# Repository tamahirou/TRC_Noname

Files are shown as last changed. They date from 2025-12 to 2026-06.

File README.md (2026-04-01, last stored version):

# TRC2027基板回路図説明書

### 0.これは回路図段階で書いたものです
# 1.メイン基板について
### 1-1.電源ブロック
DCDCコンバーターについて
| 使用モジュール | 元電源電圧 | 変換電源電圧 | 最大電流 |
| :--- | :--- | :--- | :--- |
| LMR38025 | 22.2V~25.2V | 5V | 3A |
| OKL-T/6-W12N-C | 5V | 3.3V | 6A |

電源接続コネクタ : XT90

電源最大許容電流 : 10A それ以上になるとヒューズで切れます

逆接保護 : SBDとヒューズ　逆接時ショート状態になった後ヒューズが切れることにより安全に遮断

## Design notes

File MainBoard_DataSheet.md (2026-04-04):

# TRC2027MainBoard_DataSheet

### 0.これは回路図段階で書いたものです
# 1.メイン基板について
### 1-1.電源ブロック
#### DCDCコンバーターについて
| 使用モジュール | 元電源電圧 | 変換電源電圧 | 最大電流 |
| :--- | :--- | :--- | :--- |
| LMR38025 | 22.2V~25.2V | 5V | 3A |
| OKL-T/6-W12N-C | 5V | 3.3V | 6A |

#### 電圧表示機

絶縁型DCDCコンバーターで5Vから新たな5VとGNDを生成しそれを用いることで別GNDとして電圧表示機を動作させる

#### その他

電源接続コネクタ : XT90

電源最大許容電流 : 10A それ以上になるとヒューズで切れます

逆接保護 : SBDとヒューズ　逆接時ショート状態になった後ヒューズが切れることにより安全に遮断

### 1-2.モータードライバー(DRV8262DDWRModule)

自作をしました、モジュールについては2をご覧ください

XH出力　最大電流3A

| 題 | 値 |
| :--- | :--- |
| AIN1 | GPIO6 |
| AIN2 | GPIO7 |
| BIN1 | GPIO8 |
| BIN2 | GPIO9 |
| CIN1 | GPIO10 |
| CIN2 | GPIO11 |
| DIN1 | GPIO13 |
| DIN2 | GPIO14 |
### 1-3.BNO055
| 題 | 値 |
| :--- | :--- |
| 電源電圧 | 3.3V |
| 通信方法 | I2C |
| 通信ポート | GPIO2,3|

### 1-4.GPS(MIKROE-5914)
| 題 | 値 |
| :--- | :--- |
| 電源電圧 | 5V |
| 通信方法 | I2C |
| 通信ポート | GPIO2,3 |
| リセットピン | GPIO15 |

### 1-5.気温気圧高度センサー(回路図ブロック名:Temperature, pressure, and altitude sensor)
| 題 | 値 |
| :--- | :--- |
| 電源電圧 | 5V |
| 通信方法 | I2C |
| 通信ポート | GPIO2,3 |

### 1-6.SD
| 題 | 値 |
| :--- | :--- |
| 電源電圧 | 3.3V |
| 通信方法 | SPI |
| 通信ピン | 以下の通り |
| SCK | GPIO18 |
| MISO | GPIO16 |
| MOSI | GPIO19 |
| CS | GPIO17 |

### 1-7.Lora
| 題 | 値 |
| :--- | :--- |
| 電源電圧 | 5V |
| 通信方法 | UART (1) |
| 通信ポート | GPIO4,5 |
| AUX(状態表示ピン) | GPIO12 |

モード選択:通常送受信モード: M0,M1ともにLow

### 1-8.LiDAR
| 題 | 値 |
| :--- | :--- |
| 電源電圧 | 5V |
| 通信方法 | I2C |
| 通信方法 | GPIO2,3 |

### 1-9.Camera(UnitV2 M12)
| 題 | 値 |
| :--- | :--- |
| 電源電圧 | 5V |
| 通信方法 | UART (0) |
| 通信ポート | GPIO0,1 |

### 1-10.NFC/Felica
| 題 | 値 |
| :--- | :--- |
| 電源電圧 | 5V |
| 通信方法 | I2C |
| 通信ポート | GPIO2,3 |
| 安定化 | 5VとGND間すぐに47μF |

### 1-11.FullColorLED
| 題 | 値 |
| :--- | :--- |
| 追加できるポート | なし |
### 1-12.I2C⇔UART変換
| 題 | 値 |
| :--- | :--- |
| 目的 | LTE対応のため |
| マイコン通信 | I2C |
| マイコン通信ポート | GPIO2,3 |
| LTEとの通信 | UART |
| LTEとの通信ポート | 左側7,8番ピン |

### 1-13.LTE
| 題 | 値 |
| :--- | :--- |
| 電源電圧 | 5V |
| VIO電圧 | 3.3V |
| 電源注意事項 | VINとVIOのジャンパを外す |
| RESETピン | GPIO26 |
| PWRKEYピン | GPIO27 |
| PWRKEYとは | 一定時間Lowにすると起動 |
| RESETピン＆PWRKEY | Lowにすると起動 | 
| 通信方法 | UART |
| 通信ピン | 1-12のもの |

詳しくは予算表を

# 2.自作モータードライバー基板について(DRV8262DDWModule)
| 題 | 値 | 値2 | 値3 | 値4 |
| :--- | :--- | :--- | :--- | :--- |
|仕様定義名|数値|
|定格電圧|25V|
|推奨動作電圧|24V|
|絶対最大定格電圧|50V|
|ピーク電流|16A|
|推奨連続動作電流|6A以下|
|ロジック電圧|3.3V or 5V|
|最大電流設定|無効化(フルパワー出力)|
|DECAYモード|スローディケイ(ブレーキまたはハイサイド還流)
|PWMオフ時間(TOFFピン)|7μs(TOFFをGNDに接地)|
|フォルトからの回復方法|自動的に通常動作に復帰|
|フォルト通知|VM定電流|VCP定電圧|過電流|サーマルシャットダウン|
|ブリッジモード|シングルHブリッジ|
|制御方法|PWM制御|
|nSLEEPピンの状態|常にHigh→デバイスが常にイネーブル|
|サーマルパッド|GND接続|
|安定化コンデンサ|470μF|100μなどでもいいですが、6Aまで持たせるため470μ|
|おすすめ銅箔の厚さ|2oz|
|ビア処理|レジスト開口|
|熱耐久|理論上は6A30分でも熱保護働かず耐え|
|VM,GNDコネクタ|XT30|
|OUT1,2コネクタ|XT30|
|その他コネクタ|JST XHコネクタ|
|熱対策|サーマルビアをパッドに32個|様々な配線にサーマルビア|

## ICのデータシート
[https://www.ti.com/document-viewer/ja-jp/DRV8262/datasheet]

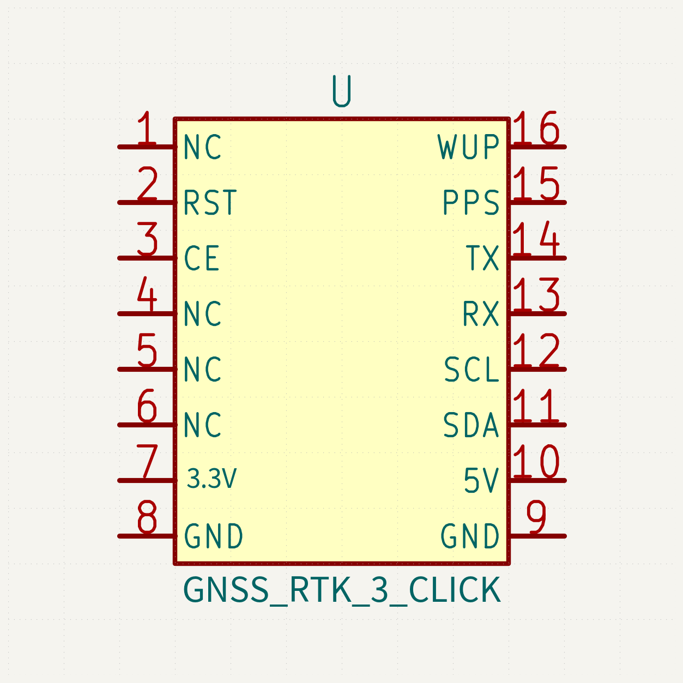
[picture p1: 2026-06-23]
TRC2027/TRC2027main2/GNSSRTK3/previews/GNSS_RTK_3_Click_symbol_preview.png

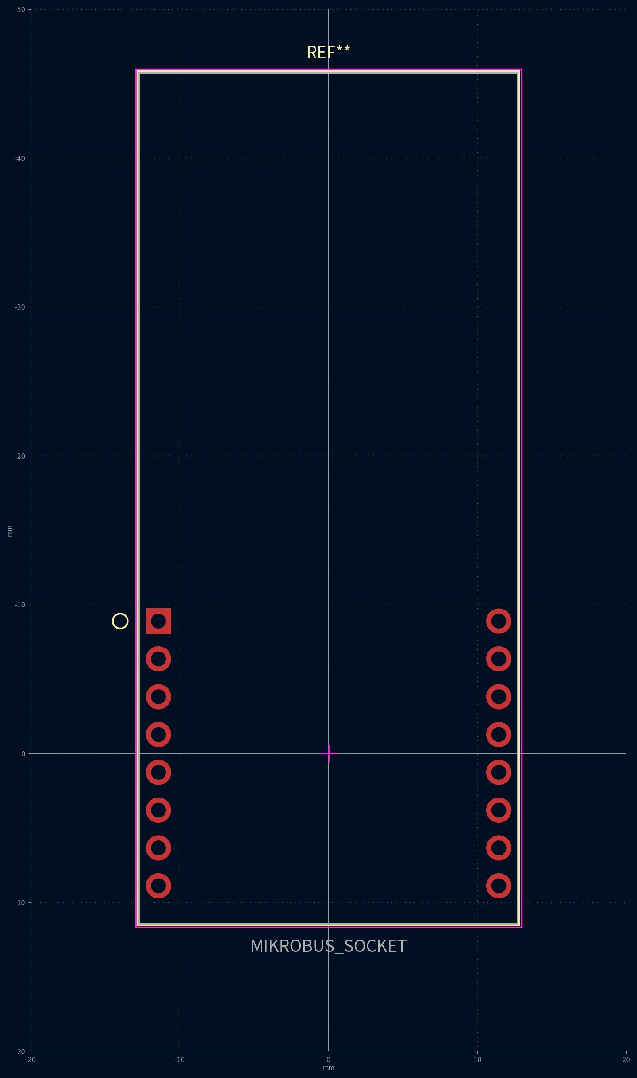
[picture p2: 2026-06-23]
TRC2027/TRC2027main2/GNSSRTK3/previews/MIKROBUS_SOCKET_footprint_preview.png

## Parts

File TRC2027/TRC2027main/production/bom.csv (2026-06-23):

Designator | Footprint | Quantity | Value | LCSC Part #
AMOTER, CMOTER, J5 | JST_XH_B2B-XH-A_1x02_P2.50mm_Vertical | 3 | XH_Moter_Output
C1 | CAPPRD500W65D1000H1300 | 1 | 470μF
C11, C9 | CP_Radial_D8.0mm_P3.50mm | 2 | 100u
C2, C5_0.1U | 0603 | 2 | 0.1μF
C4 | CP_Radial_D8.0mm_P3.50mm | 1 | 100μF
C6 | 0603 | 1 | 22u
C7 | CP_Radial_D8.0mm_P3.50mm | 1 | C7_100u
C8 | 0603 | 1 | 10u
D1 | LED_D5.0mm | 1 | 5V抵抗内蔵
D2 | LED_D5.0mm | 1 | 3.3V抵抗内蔵
D8 | TO255P480X1000X2050-3P | 1 | MBR3045FCT
DMOTER | JST_XH_B2B-XH-A_1x02_P2.50mm_Vertical | 1 | DMoter
F2 | FUSE_3557-15 | 1 | 3557-15
J1 | AMASS_XT90PW-M_1x02_P10.90mm_Horizontal | 1 | Power_conn(XT90)
J28 | JST_XH_B3B-XH-A_1x03_P2.50mm_Vertical | 1 | Servo_1
J30 | JST_XH_B20B-XH-A_1x20_P2.50mm_Vertical | 1 | Conn_01x20_Pin
MD1 | OKL-T&slash_6-W12N-C-Kai | 1 | OKL-T_6-W12N-C | OKL-T/6-W12N-C
PS1 | MAU101 | 1 | MAU102_電圧計用切り離し
R1 | R_Axial_DIN0207_L6.3mm_D2.5mm_P10.16mm_Horizontal | 1 | 1.5k
R2 | R_Axial_DIN0207_L6.3mm_D2.5mm_P10.16mm_Horizontal | 1 | 680
R3 | R_Axial_DIN0207_L6.3mm_D2.5mm_P10.16mm_Horizontal | 1 | 1.2k
SERVO_2, SERVO_3 | JST_XH_B3B-XH-A_1x03_P2.50mm_Vertical | 2 | Conn_01x03_Pin
SW1 | AMASS_XT90PW-M_1x02_P10.90mm_Horizontal | 1 | SW_SPST
U1 | LM70880Module | 1 | ~
U2, U3, U4, U5 | DRV8262DDWRModule | 4 | DRV8262DDWR
測定電圧 | JST_XH_B2B-XH-A_1x02_P2.50mm_Vertical | 1 | 電圧計_測定
電源供給 | JST_XH_B2B-XH-A_1x02_P2.50mm_Vertical | 1 | 電圧計_電源

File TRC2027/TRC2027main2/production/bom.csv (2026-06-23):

Designator | Footprint | Quantity | Value | LCSC Part #
_2, |  | 2
A1 | RaspberryPi_Pico_Common_Unspecified | 1 | RaspberryPi_Pico
C3 | CP_Radial_D5.0mm_P2.00mm | 1 | 47u
D10, D11, D12, D13, D3, D4, D5, D6, D7, D9 | UCLAMP3381PTFT | 10 | UCLAMP3381P.TFT
IC1 | DIP794W56P254L3486H508Q28N | 1 | MCP23017-E_SP
J10 | PinSocket_1x07_P2.54mm_Vertical | 1 | Memory
J11, J7 | PinSocket_1x04_P2.54mm_Vertical | 2 | BNO055
J12 | PinSocket_1x07_P2.54mm_Vertical | 1 | Temperature, pressure, and altitude sensor
J13 | PinHeader_1x03_P2.54mm_Vertical | 1 | Conn_01x03_Pin
J14, J15, J16, J17, J18, J21, J24, J25 | JST_XH_B4B-XH-A_1x04_P2.50mm_Vertical | 8 | Conn_01x04_Pin
J19 | PinHeader_1x12_P2.54mm_Vertical | 1 | Conn_01x12_Pin
J20 | PinHeader_1x10_P2.54mm_Vertical | 1 | Conn_01x10_Pin
J30 | JST_XH_B20B-XH-A_1x20_P2.50mm_Vertical | 1 | Conn_01x20_Pin
J6 | PinHeader_1x07_P2.54mm_Vertical | 1 | Conn_01x07_Pin
J8, J9 | PinHeader_1x08_P2.54mm_Vertical | 2 | Conn_01x08_Pin
R10 | R_Axial_DIN0207_L6.3mm_D2.5mm_P10.16mm_Horizontal | 1 | 75
R11 | R_Axial_DIN0207_L6.3mm_D2.5mm_P10.16mm_Horizontal | 1 | 10k
R4, R9 | R_Axial_DIN0207_L6.3mm_D2.5mm_P10.16mm_Horizontal | 2 | 330
R5, R6, R7, R8 | R_Axial_DIN0207_L6.3mm_D2.5mm_P10.16mm_Horizontal | 4 | 10
S1 | ST12303FCG | 1 | ST12-303FCG

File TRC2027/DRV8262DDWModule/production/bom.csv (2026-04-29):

Designator | Footprint | Quantity | Value | LCSC Part #
C1 | 0603 | 1 | 1u
C2 | 0603 | 1 | 0.01u
C3 | CP_Radial_D10.0mm_P5.00mm | 1 | 470u
C4 | 0603 | 1 | 0.1u
D1 | LED_D5.0mm | 1 | LED
J1, J2 | AMASS_XT30PW-F_1x02_P2.50mm_Horizontal | 2 | XT30
J3 | JST_XH_B5B-XH-A_1x05_P2.50mm_Vertical | 1 | Conn_01x05_Pin
R1 | 1206 | 1 | 10k
R2 | R_Axial_DIN0207_L6.3mm_D2.5mm_P10.16mm_Horizontal | 1 | 4.7k
U1 | HTSSOP44-DDW_TEX | 1 | DRV8262DDWR

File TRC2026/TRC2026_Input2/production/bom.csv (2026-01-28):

Designator | Footprint | Quantity | Value | LCSC Part #
C3 | 0603 | 1 | 0.1μF
D15 | LED_D5.0mm | 1 | 5V抵抗内蔵LED
D2, D7 | LED_D5.0mm | 2 | BLUELED
D3, D4 | LED_D5.0mm | 2 | GREENLED
D5, D6 | LED_D5.0mm | 2 | REDLED
J1 | PinHeader_1x06_P2.54mm_Vertical | 1 | ジョイスティック
J2 | PinHeader_1x06_P2.54mm_Vertical | 1 | Conn_01x06_Pin
J3, J5, J6 | PinHeader_1x05_P2.54mm_Vertical | 3 | Conn_01x05_Pin
J4 | PinHeader_1x05_P2.54mm_Vertical | 1 | 1F接続
R10, R11, R12, R9 | R_Axial_DIN0207_L6.3mm_D2.5mm_P10.16mm_Horizontal | 4 | 10Ω
R7, R8 | R_Axial_DIN0207_L6.3mm_D2.5mm_P10.16mm_Horizontal | 2 | 470Ω
SW1, SW2, SW3, SW4 | TVGP01G73BB | 4 | SW_Push
SW5 | 3MS1J102M2QES | 1 | SW_SPDT

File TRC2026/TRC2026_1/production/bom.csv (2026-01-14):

Designator | Footprint | Quantity | Value | LCSC Part #
A1 | RaspberryPi_Pico_Common_Unspecified | 1 | RaspberryPi_Pico
A2 | RaspberryPi_PicoW_Common_THT | 1 | RaspberryPi_Pico_W
C1, C6, C7, C8 | CP_Radial_D8.0mm_P3.50mm | 4 | 100μF
C3 | 0603 | 1 | 0.1μF
D10, D11, D12, D13, D14, D9 | SOD2513X114N | 6 | UCLAMP3381P.TFT
D15 | LED_D5.0mm | 1 | 5V抵抗内蔵LED
J1, J15, J16, J17 | PinHeader_1x04_P2.54mm_Vertical | 4 | 2F接続
J10 | PinSocket_1x07_P2.54mm_Vertical | 1 | メモリ
J11 | PinSocket_1x04_P2.54mm_Vertical | 1 | BNO055
J12 | PinSocket_1x07_P2.54mm_Vertical | 1 | 気温気圧高度センサ
J13, J14, J18 | JST_XH_B4B-XH-A_1x04_P2.50mm_Vertical | 3 | Conn_01x04_Pin
J19 | JST_XH_B3B-XH-A_1x03_P2.50mm_Vertical | 1 | サーボ1
J2 | PinHeader_1x08_P2.54mm_Vertical | 1 | Aモータードライバー
J20 | JST_XH_B3B-XH-A_1x03_P2.50mm_Vertical | 1 | サーボ2
J21 | JST_XH_B3B-XH-A_1x03_P2.50mm_Vertical | 1 | サーボ3(予備)
J22 | PinSocket_1x12_P2.54mm_Vertical | 1 | LoRa
J23 | PinSocket_1x12_P2.54mm_Vertical | 1 | Conn_01x12_Pin
J3 | JST_XH_B2B-XH-A_1x02_P2.50mm_Vertical | 1 | Aモーター出力
J4 | PinHeader_1x08_P2.54mm_Vertical | 1 | Bモータードライバー
J5 | JST_XH_B2B-XH-A_1x02_P2.50mm_Vertical | 1 | Bモーター出力
J6 | PinHeader_1x04_P2.54mm_Vertical | 1 | Conn_01x04_Pin
J7 | PinSocket_1x04_P2.54mm_Vertical | 1 | GPS
J8, J9 | PinHeader_1x08_P2.54mm_Vertical | 2 | Conn_01x08_Pin
R1, R4 | R_Axial_DIN0207_L6.3mm_D2.5mm_P10.16mm_Horizontal | 2 | 1.5Ω
R2, R3, R5, R6 | 1210 | 4 | 0.1Ω

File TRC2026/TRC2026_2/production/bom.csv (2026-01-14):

Designator | Footprint | Quantity | Value | LCSC Part #
C1 | CAPPRD500W65D1000H1300 | 1 | 470μF
C2, C5 | 0603 | 2 | 0.1μF
C4 | CP_Radial_D8.0mm_P3.50mm | 1 | 100μF
D1 | LED_D5.0mm | 1 | 5V抵抗内蔵LED
D2, D3, D4, D5, D6, D7 | LED_D5.0mm | 6 | LED
D8 | TO255P480X1000X2050-3P | 1 | MBR3045FCT
F2 | FUSE_3557-15 | 1 | 3557-15
J1 | AMASS_XT90PW-M_1x02_P10.90mm_Horizontal | 1 | Conn_01x02_Pin
J15 | PinSocket_1x04_P2.54mm_Vertical | 1 | Conn_01x04_Pin
J16 | JST_XH_B2B-XH-A_1x02_P2.50mm_Vertical | 1 | デジタル電圧計(測定)
J17 | JST_XH_B2B-XH-A_1x02_P2.50mm_Vertical | 1 | デジタル電圧計(電力供給)
J2, J3, J4, J5, J6 | PinHeader_1x04_P2.54mm_Vertical | 5 | Conn_01x04_Pin
R10, R11, R12, R9 | R_Axial_DIN0207_L6.3mm_D2.5mm_P10.16mm_Horizontal | 4 | 10Ω
R13 | R_Axial_DIN0516_L15.5mm_D5.0mm_P20.32mm_Horizontal | 1 | 0.33Ω(熱くなります。基板取り付け時は地面から離しましょう)
R7, R8 | R_Axial_DIN0207_L6.3mm_D2.5mm_P10.16mm_Horizontal | 2 | 470Ω
SW1 | AMASS_XT90PW-M_1x02_P10.90mm_Horizontal | 1 | SW_SPST
SW2 | 3MS1J102M2QES | 1 | SW_SPDT
U1 | LMR | 1 | DCDC

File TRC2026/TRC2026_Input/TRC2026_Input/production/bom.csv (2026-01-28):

Designator | Footprint | Quantity | Value | LCSC Part #
A1 | RaspberryPi_Pico_Common_Unspecified | 1 | RaspberryPi_Pico_W
C1, C6 | 0603 | 2 | 0.1μF
C2, C4, C5 | CP_Radial_D8.0mm_P3.50mm | 3 | 100μF
J22 | PinSocket_1x12_P2.54mm_Vertical | 1 | LoRa
J23 | PinSocket_1x12_P2.54mm_Vertical | 1 | Conn_01x12_Pin
J3, J4, J5, J6 | PinHeader_1x05_P2.54mm_Vertical | 4 | 2F接続

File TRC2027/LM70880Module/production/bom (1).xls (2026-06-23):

Comment | Designator | Footprint | JLCPCB Part #
LM70880RRXR | U1 | RRX0029B-MFG | C41525220
47n | C10 | 0603 | C1622
19.1k | R4 | 0603 | C22897
24.9k | R3 | 0603 | C25962
5m | R9 | 1206 | C7419996
6.8n | C7 | 0603 | C1631
4.7u | C1,C2,C3,C4,C6 | 0805 | C76651
3.3u | L1 | SMMS10505R6M | C128687
Conn_01x02_Pin | J1,J2 | AMASS_XT30PW-F_1x02_P2.50mm_Horizontal | C2913282
1 | R8 | 0603 | C22936
47p | C8 | 0603 | C1671
5.76k | R5 | 0603 | C2933239
0.1u | C5,C9 | 0603 | C14663
47u | C11,C12,C13,C14 | 0603 | C140782
54.9k | R7 | 0603 | C23077
29.4k | R6 | 0603 | C2930086
100k | R1 | 0603 | C25803
20.5k | R2 | 0603 | C2930074

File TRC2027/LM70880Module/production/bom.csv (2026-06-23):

Designator | Footprint | Quantity | Value | LCSC Part #
C1, C2, C3, C4, C6 | 0805 | 5 | 4.7u
C10 | 0603 | 1 | 47n
C11, C12, C13, C14 | 0603 | 4 | 47u
C5, C9 | 0603 | 2 | 0.1u
C7 | 0603 | 1 | 6.8n
C8 | 0603 | 1 | 47p
J1, J2 | AMASS_XT30PW-F_1x02_P2.50mm_Horizontal | 2 | Conn_01x02_Pin
L1 | SMMS10505R6M | 1 | 3.3u
R1 | 0603 | 1 | 100k
R2 | 0603 | 1 | 20.5k
R3 | 0603 | 1 | 24.9k
R4 | 0603 | 1 | 19.1k
R5 | 0603 | 1 | 5.76k
R6 | 0603 | 1 | 29.4k
R7 | 0603 | 1 | 54.9k
R8 | 0603 | 1 | 1
R9 | 1206 | 1 | 5m
U1 | RRX0029B-MFG | 1 | LM70880RRXR

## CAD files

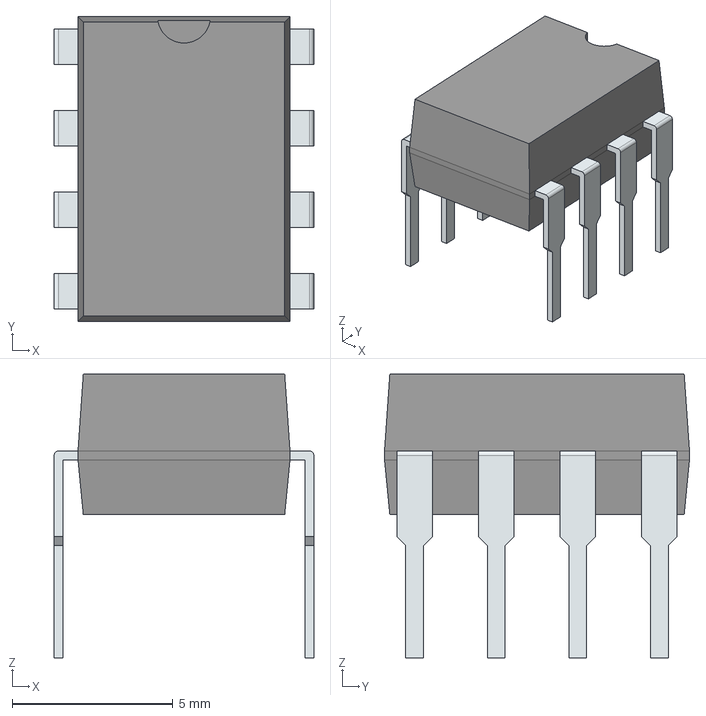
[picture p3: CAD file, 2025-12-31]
TRC2026/TRC2026_1/KiCad_24FC1025-I_P/3D/24FC1025-I_P.stp
8.09 x 9.50 x 8.83 mm
PinsArrayLR

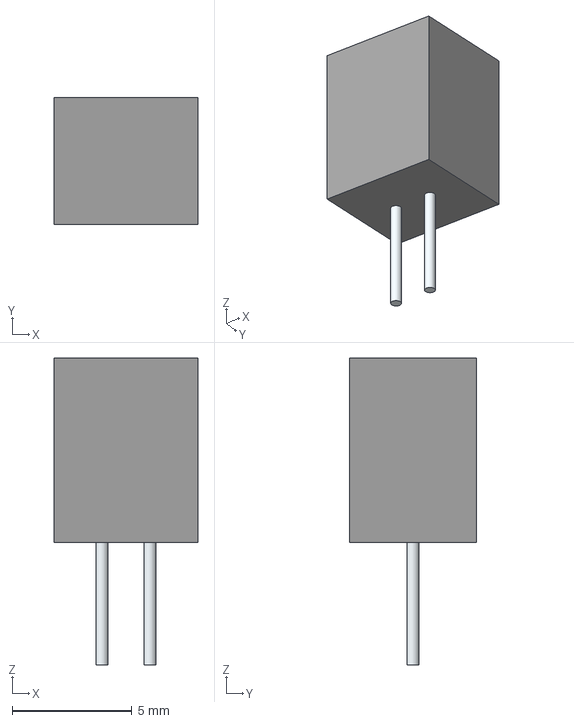
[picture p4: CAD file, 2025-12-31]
TRC2026/TRC2026_1/Kicad_B02B-PASK_LF__SN_/3D/B02B-PASK_LF__SN_.stp
6.00 x 5.30 x 12.8 mm
Leads

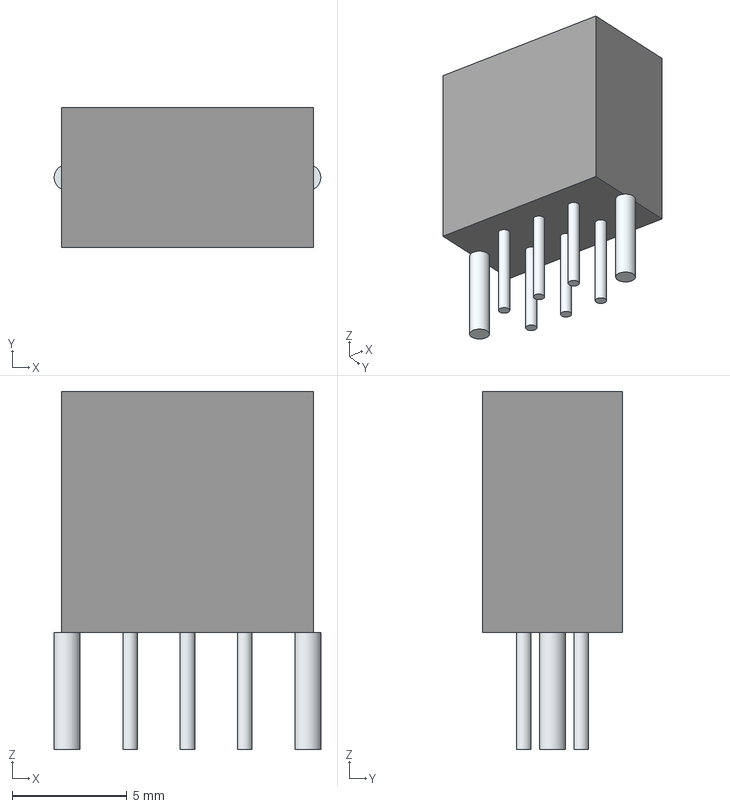
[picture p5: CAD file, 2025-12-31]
TRC2026/TRC2026_1/Kicad_switch_SS22E01G5-HA-G/3D/SS22E01G5-HA-G.stp
11.6 x 6.10 x 15.6 mm
Leads

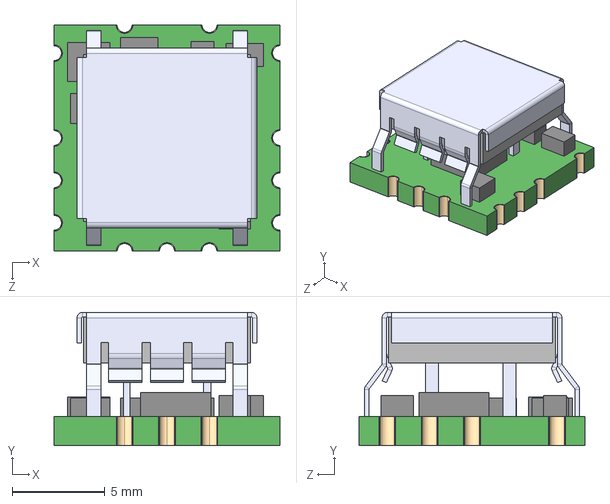
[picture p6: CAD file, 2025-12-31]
TRC2026/TRC2026_1/OKL_T_6_W12N_C/OKL-T_6-W12N-C.step
12.2 x 7.20 x 12.2 mm

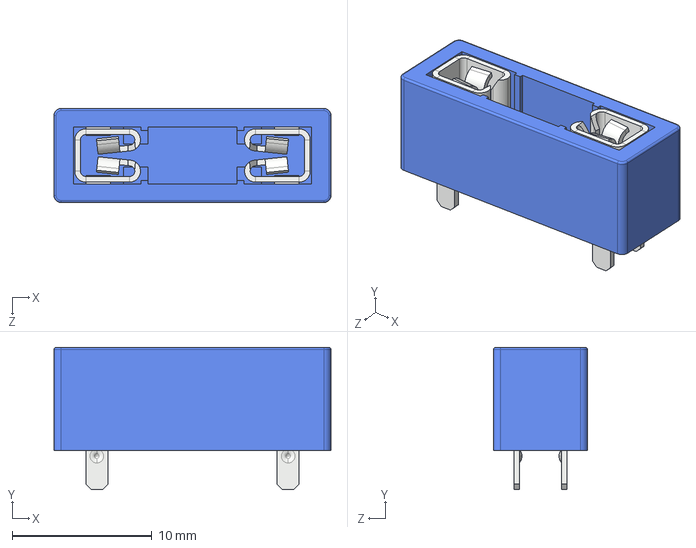
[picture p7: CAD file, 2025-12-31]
TRC2027/TRC2027main2/3557-15_fuse/3557-15.step
19.8 x 10.2 x 6.73 mm

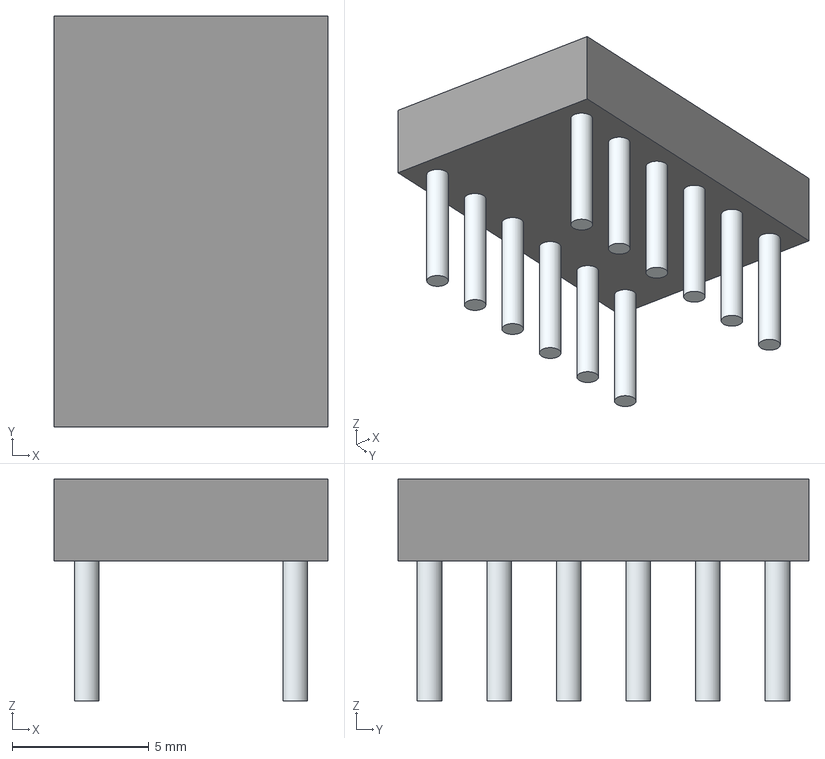
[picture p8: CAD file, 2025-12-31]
TRC2027/TRC2027main2/KiCad_DRV8835/AE-DRV8835-S.stp
10.0 x 15.0 x 8.10 mm
Leads

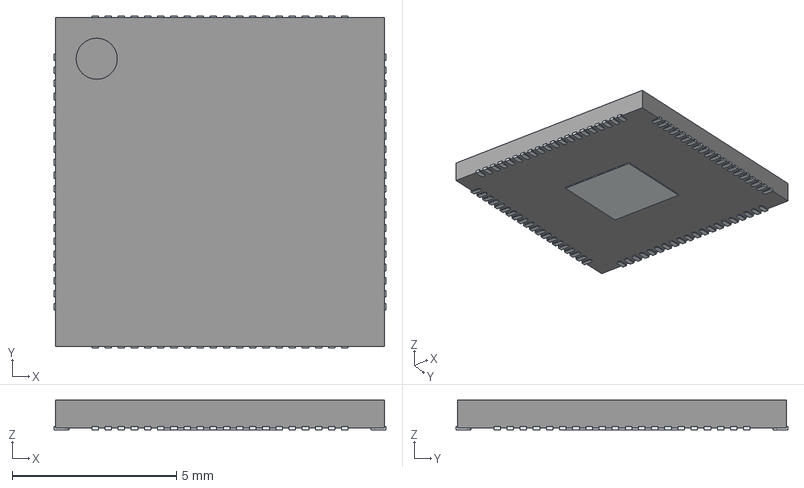
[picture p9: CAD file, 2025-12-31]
TRC2027/TRC2027main2/KiCad_RP2350B/RP2350B.stp
10.1 x 10.1 x 0.9 mm
ThermalPin
PinsArrayLR
PinsArrayTB

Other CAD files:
TRC2026/TRC2026_1/KiCad_24FC1025-I_P/Allegro/dip781w56p254l950h533q8n.psm
TRC2026/TRC2026_1/KiCad_24FC1025-I_P/DEHDL/24fc1025_i_p/chips/chips.prt
TRC2026/TRC2026_1/Kicad_B02B-PASK_LF__SN_/DEHDL/b02b_pask_lf__sn_/chips/chips.prt
TRC2026/TRC2026_1/Kicad_switch_SS22E01G5-HA-G/Allegro/ss22e01g5hag.psm
TRC2026/TRC2026_1/Kicad_switch_SS22E01G5-HA-G/DEHDL/ss22e01g5_ha_g/chips/chips.prt
TRC2026/TRC2026_2/KiCad_24FC1025-I_P/Allegro/dip781w56p254l950h533q8n.psm
TRC2026/TRC2026_2/KiCad_24FC1025-I_P/DEHDL/24fc1025_i_p/chips/chips.prt
TRC2026/TRC2026_2/Kicad_B02B-PASK_LF__SN_/DEHDL/b02b_pask_lf__sn_/chips/chips.prt
TRC2026/TRC2026_2/Kicad_switch_SS22E01G5-HA-G/Allegro/ss22e01g5hag.psm
TRC2026/TRC2026_2/Kicad_switch_SS22E01G5-HA-G/DEHDL/ss22e01g5_ha_g/chips/chips.prt
TRC2027/TRC2027main/KiCad_24FC1025-I_P/Allegro/dip781w56p254l950h533q8n.psm
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

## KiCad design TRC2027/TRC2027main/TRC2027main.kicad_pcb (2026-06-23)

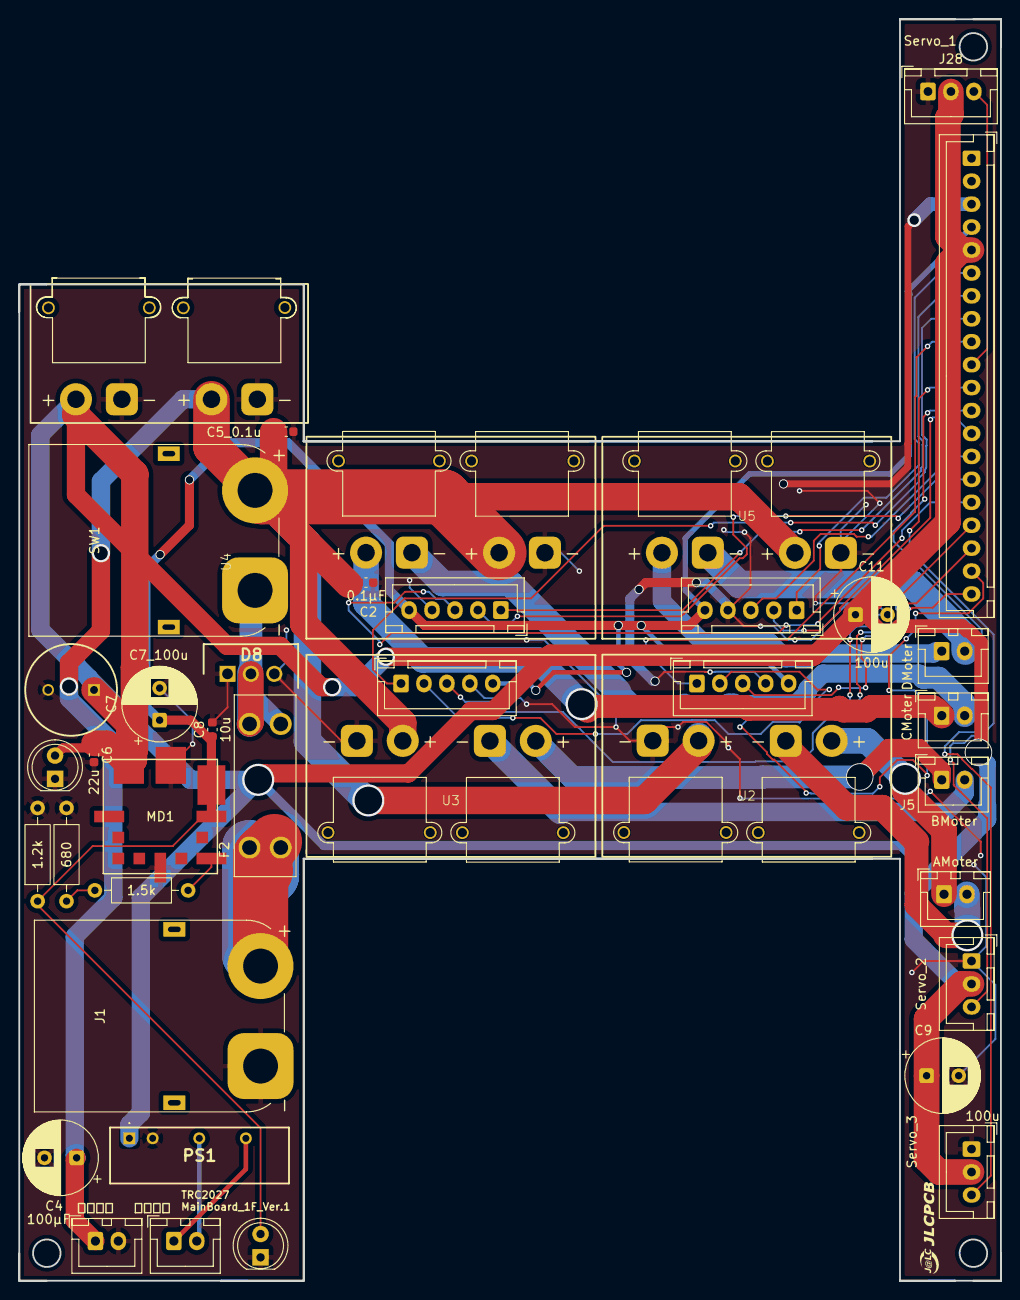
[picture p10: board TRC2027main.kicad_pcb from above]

Board: 2 copper layers, 107.0 x 137.5 mm, 35 parts (0 on the bottom side), 33 nets.

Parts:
AMoter: XH_Moter_Output; JST_XH_B2B-XH-A_1x02_P2.50mm_Vertical
C1: 470μF; CAPPRD500W65D1000H1300
C2, C5_0.1u: 0.1μF; C_0603_1608Metric
C4: 100μF; CP_Radial_D8.0mm_P3.50mm
C6: 22u; C_0603_1608Metric
C7: C7_100u; CP_Radial_D8.0mm_P3.50mm
C8: 10u; C_0603_1608Metric
C9, C11: 100u; CP_Radial_D8.0mm_P3.50mm
CMoter: XH_Moter_Output; JST_XH_B2B-XH-A_1x02_P2.50mm_Vertical
D1: 5V抵抗内蔵; LED_D5.0mm
D2: 3.3V抵抗内蔵; LED_D5.0mm
D8: MBR3045FCT; TO255P480X1000X2050-3P
DMoter: DMoter; JST_XH_B2B-XH-A_1x02_P2.50mm_Vertical
F2: 3557-15; FUSE_3557-15
J1: Power_conn(XT90); AMASS_XT90PW-M_1x02_P10.90mm_Horizontal
J5: XH_Moter_Output; JST_XH_B2B-XH-A_1x02_P2.50mm_Vertical
J28: Servo_1; JST_XH_B3B-XH-A_1x03_P2.50mm_Vertical
J30: Conn_01x20_Pin; JST_XH_B20B-XH-A_1x20_P2.50mm_Vertical
MD1: OKL-T_6-W12N-C; OKL-T&slash_6-W12N-C-Kai
PS1: MAU102_電圧計用切り離し; MAU101
R1: 1.5k; R_Axial_DIN0207_L6.3mm_D2.5mm_P10.16mm_Horizontal
R2: 680; R_Axial_DIN0207_L6.3mm_D2.5mm_P10.16mm_Horizontal
R3: 1.2k; R_Axial_DIN0207_L6.3mm_D2.5mm_P10.16mm_Horizontal
SW1: SW_SPST; AMASS_XT90PW-M_1x02_P10.90mm_Horizontal
Servo_2, Servo_3: Conn_01x03_Pin; JST_XH_B3B-XH-A_1x03_P2.50mm_Vertical
U1: LM70880Module
U2, U3, U4, U5: DRV8262DDWR; DRV8262DDWRModule
測定電圧: 電圧計_測定; JST_XH_B2B-XH-A_1x02_P2.50mm_Vertical
電源供給: 電圧計_電源; JST_XH_B2B-XH-A_1x02_P2.50mm_Vertical

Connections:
+3.3V: C7.1, C8.1, D2.2 (A), J30.4, MD1.4 (VOUT), MD1.5 (SENSE), R3.1, U2.9 (VCC), U3.9 (VCC), U4.9 (VCC), U5.9 (VCC)
+5V: C1.1, C6.1, C9.1, C11.1, D1.2 (A), J28.2, J30.5, MD1.2 (VIN), PS1.1 (+VIN), Servo_2.2, Servo_3.2, U1.4 (VOUT)
+5VD: PS1.6 (+VOUT), 電源供給.1
+24V: C2.1, C4.1, C5_0.1u.1, SW1.2 (B), U1.2 (VIN), U2.3 (VM), U3.3 (VM), U4.3 (VM), U5.3 (VM), 測定電圧.1
+BATT: F2.1_1, F2.1_2, J1.2
AIN1: J30.20, U2.7 (IN1)
AIN2: J30.19, U2.6 (IN2)
AOUT1: AMoter.1, U2.1 (OUT1)
AOUT2: AMoter.2, U2.2 (OUT2)
AnFAULT: J30.9, U2.5 (nFAULT)
BIN1: J30.18, U3.7 (IN1)
BIN2: J30.17, U3.6 (IN2)
BOUT1: J5.1, U3.1 (OUT1)
BOUT2: J5.2, U3.2 (OUT2)
BnFAULT: J30.8, U3.5 (nFAULT)
CIN1: J30.16, U4.7 (IN1)
CIN2: J30.15, U4.6 (IN2)
COUT1: CMoter.1, U4.1 (OUT1)
COUT2: CMoter.2, U4.2 (OUT2)
CnFAULT: J30.7, U4.5 (nFAULT)
DIN1: J30.14, U5.7 (IN1)
DIN2: J30.13, U5.6 (IN2)
DOUT1: DMoter.1, U5.1 (OUT1)
DOUT2: DMoter.2, U5.2 (OUT2)
DnFAULT: J30.6, U5.5 (nFAULT)
GND: C1.2, C2.2, C4.2, C5_0.1u.2, C6.2, C7.2, C8.2, C9.2, C11.2, D1.1 (K), D2.1 (K), D8.1 (A_1), D8.3 (A_2), J1.1, J28.1, J30.3, MD1.3 (1_GROUND), MD1.7 (2_GROUND), PS1.2 (-VIN), R2.2, R3.2, Servo_2.1, Servo_3.1, U1.1 (GND), U1.3 (GND), U2.4 (GND), U2.8 (GND), U3.4 (GND), U3.8 (GND), U4.4 (GND), U4.8 (GND), U5.4 (GND), U5.8 (GND), 測定電圧.2
GND1: PS1.4 (-VOUT), 電源供給.2
unnamed: D8.2 (K), F2.2_1, F2.2_2, SW1.1 (A)
unnamed: MD1.6 (TRIM), R1.1
unnamed: R1.2, R2.1
PWM: J30.12, Servo_3.3
PWM2: J30.11, Servo_2.3
PWM3: J28.3, J30.10

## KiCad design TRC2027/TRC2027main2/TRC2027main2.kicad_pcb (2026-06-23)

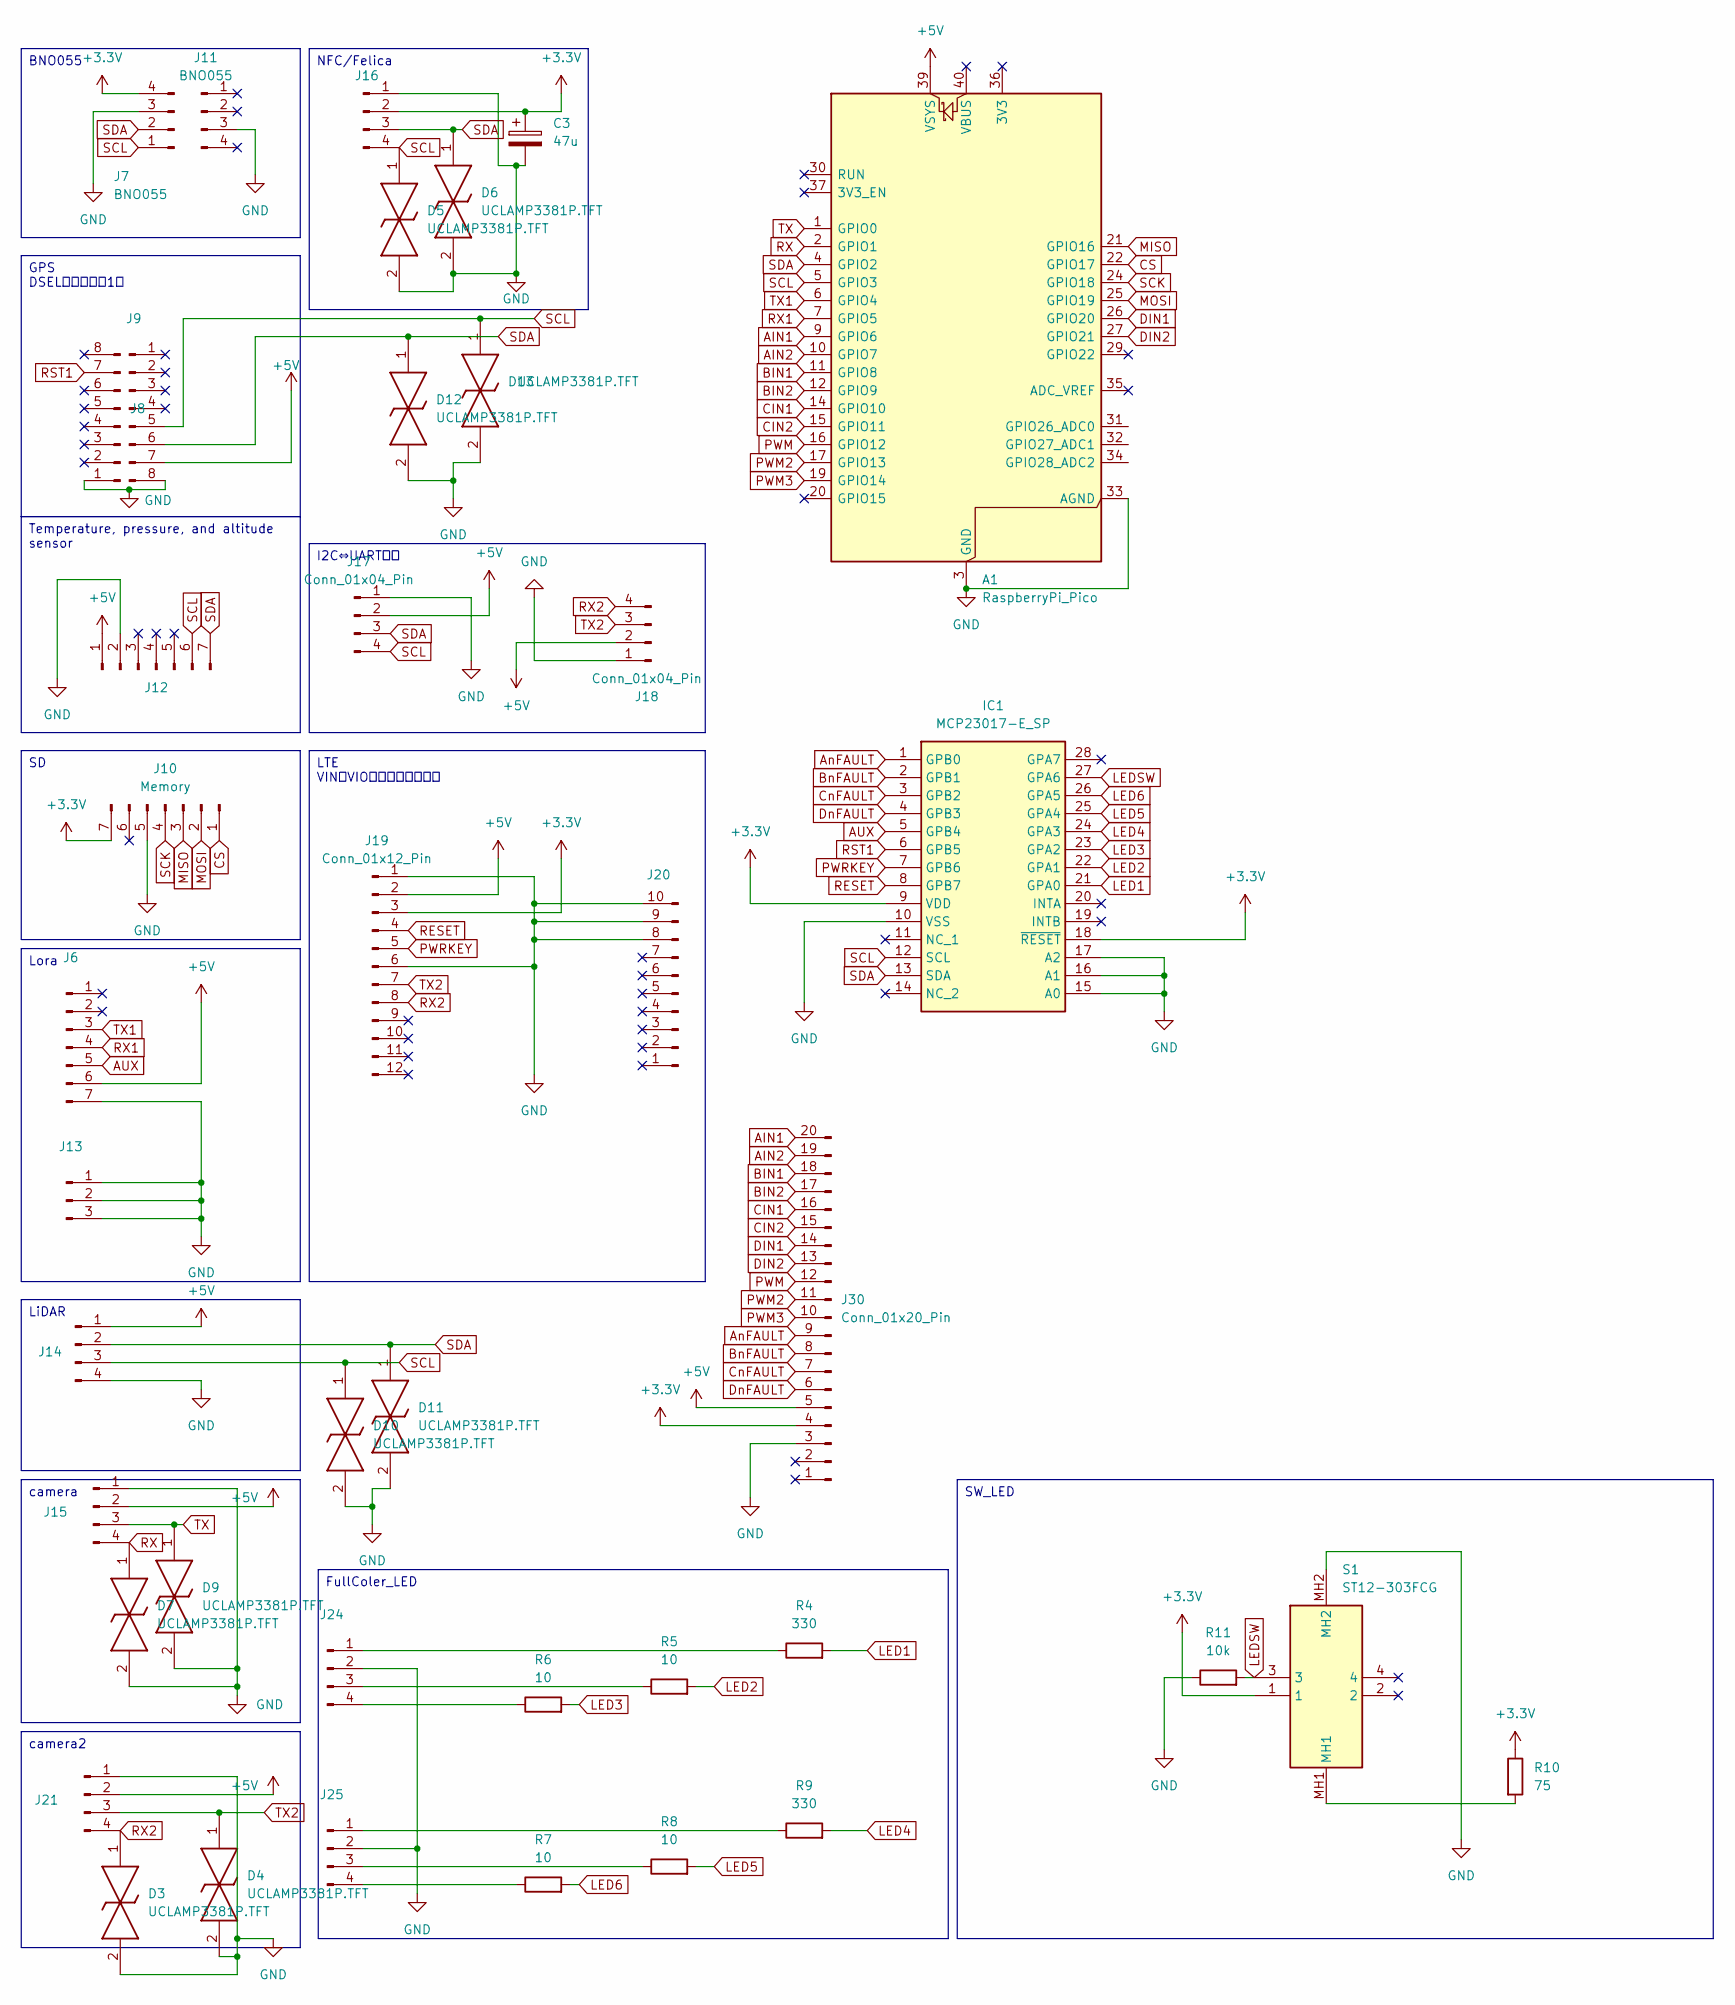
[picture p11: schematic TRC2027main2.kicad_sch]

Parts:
A1: RaspberryPi_Pico; RaspberryPi_Pico_Common_Unspecified
C3: 47u; CP_Radial_D5.0mm_P2.00mm
D3, D4, D5, D6, D7, D9, D10, D11, D12, D13: UCLAMP3381P.TFT; UCLAMP3381PTFT; Mouser Part Number 947-UCLAMP3381P.TFT
IC1: MCP23017-E_SP; DIP794W56P254L3486H508Q28N; Manufacturer_Part_Number MCP23017-E/SP; Mouser Part Number 579-MCP23017-E/SP
J6: Conn_01x07_Pin; PinHeader_1x07_P2.54mm_Vertical
J7, J11: BNO055; PinSocket_1x04_P2.54mm_Vertical
J8, J9: Conn_01x08_Pin; PinHeader_1x08_P2.54mm_Vertical
J10: Memory; PinSocket_1x07_P2.54mm_Vertical
J12: Temperature, pressure, and altitude sensor; PinSocket_1x07_P2.54mm_Vertical
J13: Conn_01x03_Pin; PinHeader_1x03_P2.54mm_Vertical
J14, J15, J16, J17, J18, J21, J24, J25: Conn_01x04_Pin; JST_XH_B4B-XH-A_1x04_P2.50mm_Vertical
J19: Conn_01x12_Pin; PinHeader_1x12_P2.54mm_Vertical
J20: Conn_01x10_Pin; PinHeader_1x10_P2.54mm_Vertical
J30: Conn_01x20_Pin; JST_XH_B20B-XH-A_1x20_P2.50mm_Vertical
R4, R9: 330; R_Axial_DIN0207_L6.3mm_D2.5mm_P10.16mm_Horizontal
R5, R6, R7, R8: 10; R_Axial_DIN0207_L6.3mm_D2.5mm_P10.16mm_Horizontal
R10: 75; R_Axial_DIN0207_L6.3mm_D2.5mm_P10.16mm_Horizontal
R11: 10k; R_Axial_DIN0207_L6.3mm_D2.5mm_P10.16mm_Horizontal
S1: ST12-303FCG; ST12303FCG; Manufacturer_Part_Number ST12-303FCG

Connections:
+3.3V: C3.1, IC1.9 (VDD), IC1.18 (~RESET), J7.4, J10.7, J16.2, J19.3, J30.4, R10.1, S1.1
+5V: A1.39 (VSYS), J6.6, J9.7, J12.1, J14.1, J15.2, J17.2, J18.2, J19.2, J21.2, J30.5
AIN1: A1.9 (GPIO6), J30.20
AIN2: A1.10 (GPIO7), J30.19
AUX: IC1.5 (GPB4), J6.5
AnFAULT: IC1.1 (GPB0), J30.9
BIN1: A1.11 (GPIO8), J30.18
BIN2: A1.12 (GPIO9), J30.17
BnFAULT: IC1.2 (GPB1), J30.8
CIN1: A1.14 (GPIO10), J30.16
CIN2: A1.15 (GPIO11), J30.15
CS: A1.22 (GPIO17), J10.1
CnFAULT: IC1.3 (GPB2), J30.7
DIN1: A1.26 (GPIO20), J30.14
DIN2: A1.27 (GPIO21), J30.13
DnFAULT: IC1.4 (GPB3), J30.6
GND: A1.3 (GND), A1.8 (GND), A1.13 (GND), A1.18 (GND), A1.23 (GND), A1.28 (GND), A1.33 (AGND), A1.38 (GND), C3.2, D3.2, D4.2, D5.2, D6.2, D7.2, D9.2, D10.2, D11.2, D12.2, D13.2, IC1.10 (VSS), IC1.15 (A0), IC1.16 (A1), IC1.17 (A2), J6.7, J7.3, J8.1, J9.8, J10.5, J11.3, J12.2, J13.1, J13.2, J13.3, J14.4, J15.1, J16.1, J17.1, J18.1, J19.1, J19.6, J20.8, J20.9, J20.10, J21.1, J24.2, J25.2, J30.3, R11.1, S1.MH2
LED1: IC1.21 (GPA0), R4.2
LED2: IC1.22 (GPA1), R5.2
LED3: IC1.23 (GPA2), R6.2
LED4: IC1.24 (GPA3), R9.2
LED5: IC1.25 (GPA4), R8.2
LED6: IC1.26 (GPA5), R7.2
LEDSW: IC1.27 (GPA6), R11.2, S1.3
MISO: A1.21 (GPIO16), J10.3
MOSI: A1.25 (GPIO19), J10.2
unnamed: J24.1, R4.1
unnamed: J24.3, R5.1
unnamed: J24.4, R6.1
unnamed: J25.1, R9.1
unnamed: J25.3, R8.1
unnamed: J25.4, R7.1
unnamed: R10.2, S1.MH1
PWM: A1.16 (GPIO12), J30.12
PWM2: A1.17 (GPIO13), J30.11
PWM3: A1.19 (GPIO14), J30.10
PWRKEY: IC1.7 (GPB6), J19.5
RESET: IC1.8 (GPB7), J19.4
RST1: IC1.6 (GPB5), J8.7
RX: A1.2 (GPIO1), D7.1, J15.4
RX1: A1.7 (GPIO5), J6.4
RX2: D3.1, J18.4, J19.8, J21.4
SCK: A1.24 (GPIO18), J10.4
SCL: A1.5 (GPIO3), D5.1, D10.1, D13.1, IC1.12 (SCL), J7.1, J9.5, J12.6, J14.3, J16.4, J17.4
SDA: A1.4 (GPIO2), D6.1, D11.1, D12.1, IC1.13 (SDA), J7.2, J9.6, J12.7, J14.2, J16.3, J17.3
TX: A1.1 (GPIO0), D9.1, J15.3
TX1: A1.6 (GPIO4), J6.3
TX2: D4.1, J18.3, J19.7, J21.3

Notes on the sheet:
Temperature, pressure, and altitude sensor
GPS DSELスイッチを1に
Lora
SW_LED
NFC/Felica
camera
LiDAR
camera2
I2C⇔UART変換
BNO055
FullColer_LED
LTE VINとVIOのジャンパを外す

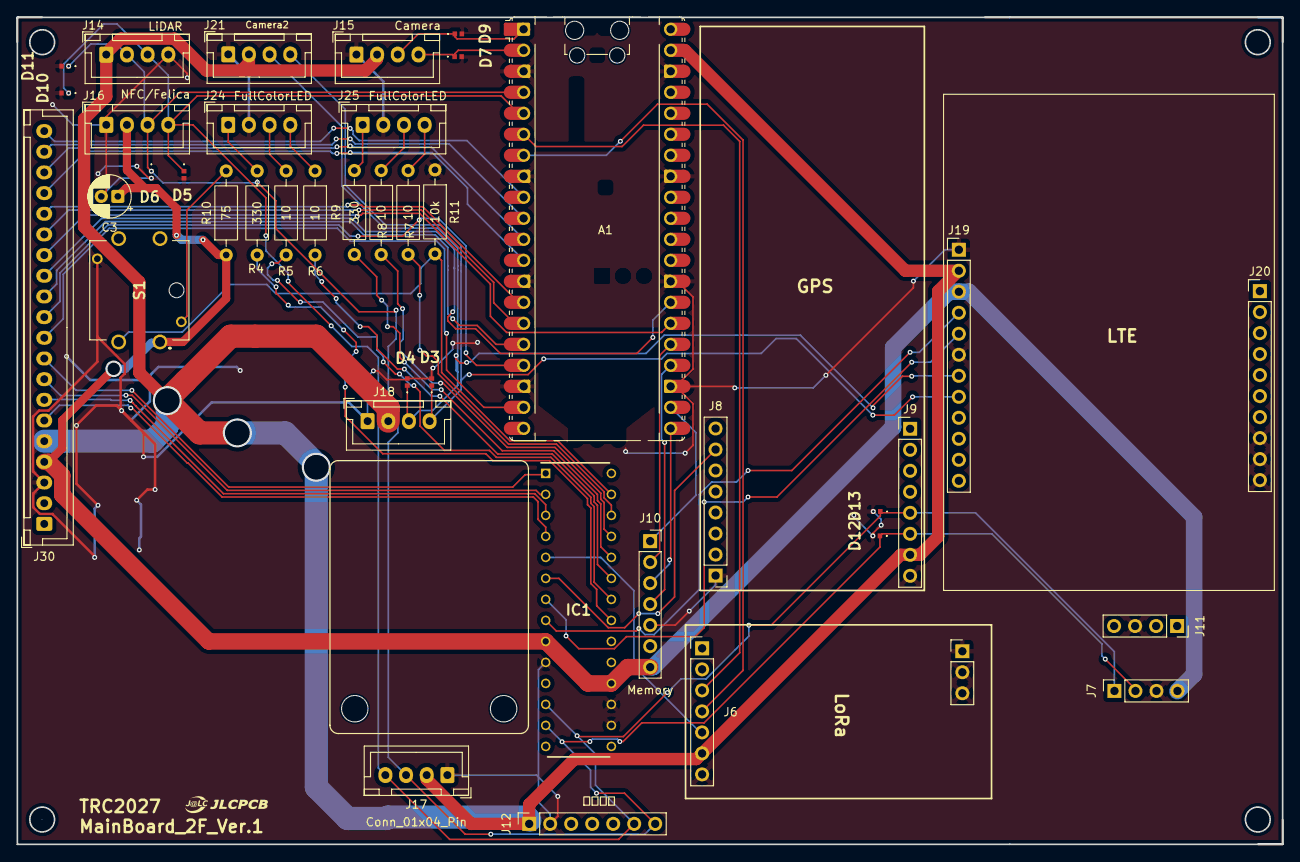
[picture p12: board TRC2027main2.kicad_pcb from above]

Board: 2 copper layers, 153.0 x 100.0 mm, 41 parts (0 on the bottom side), 48 nets.

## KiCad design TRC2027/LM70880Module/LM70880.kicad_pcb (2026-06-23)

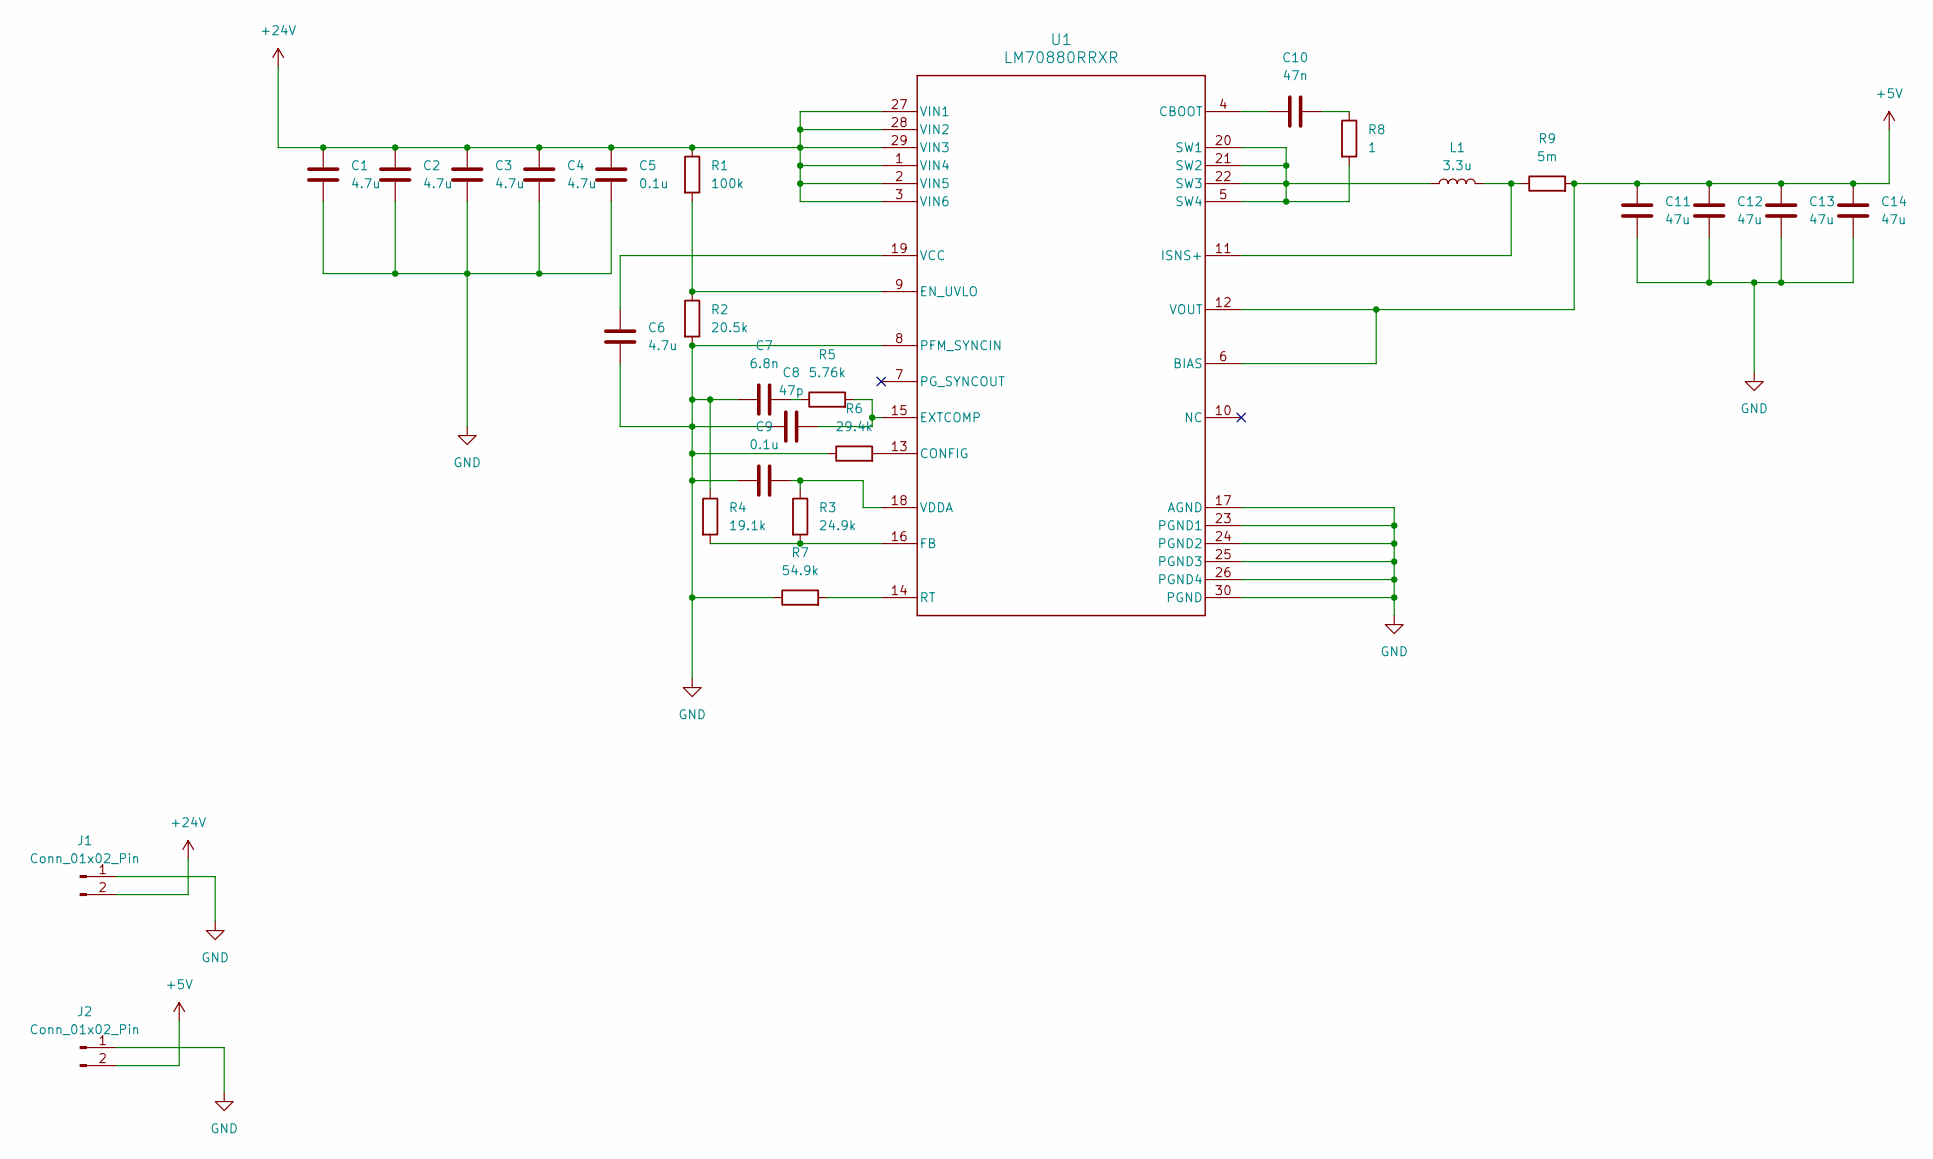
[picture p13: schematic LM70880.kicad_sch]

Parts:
C1, C2, C3, C4, C6: 4.7u; C_0805_2012Metric
C5, C9: 0.1u; C_0603_1608Metric
C7: 6.8n; C_0603_1608Metric
C8: 47p; C_0603_1608Metric
C10: 47n; C_0603_1608Metric
C11, C12, C13, C14: 47u; C_0603_1608Metric
J1, J2: Conn_01x02_Pin; AMASS_XT30PW-F_1x02_P2.50mm_Horizontal
L1: 3.3u; SMMS10505R6M
R1: 100k; R_0603_1608Metric
R2: 20.5k; R_0603_1608Metric
R3: 24.9k; R_0603_1608Metric
R4: 19.1k; R_0603_1608Metric
R5: 5.76k; R_0603_1608Metric
R6: 29.4k; R_0603_1608Metric
R7: 54.9k; R_0603_1608Metric
R8: 1; R_0603_1608Metric
R9: 5m; R_1206_3216Metric
U1: LM70880RRXR; RRX0029B-MFG

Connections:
+5V: C11.1, C12.1, C13.1, C14.1, J2.2, R9.2, U1.6 (BIAS), U1.12 (VOUT)
+24V: C1.1, C2.1, C3.1, C4.1, C5.1, J1.2, R1.1, U1.1 (VIN4), U1.2 (VIN5), U1.3 (VIN6), U1.27 (VIN1), U1.28 (VIN2), U1.29 (VIN3)
GND: C1.2, C2.2, C3.2, C4.2, C5.2, C6.2, C7.1, C8.1, C9.1, C11.2, C12.2, C13.2, C14.2, J1.1, J2.1, R2.2, R4.1, R6.1, R7.1, U1.8 (PFM_SYNCIN), U1.17 (AGND), U1.23 (PGND1), U1.24 (PGND2), U1.25 (PGND3), U1.26 (PGND4), U1.30 (PGND)
unnamed: C7.2, R5.1
unnamed: C10.2, R8.1
unnamed: C10.1, U1.4 (CBOOT)
unnamed: R6.2, U1.13 (CONFIG)
unnamed: R1.2, R2.1, U1.9 (EN_UVLO)
unnamed: C8.2, R5.2, U1.15 (EXTCOMP)
unnamed: R3.2, R4.2, U1.16 (FB)
unnamed: L1.2, R9.1, U1.11 (ISNS+)
unnamed: R7.2, U1.14 (RT)
unnamed: L1.1, R8.2, U1.5 (SW4), U1.20 (SW1), U1.21 (SW2), U1.22 (SW3)
unnamed: C6.1, U1.19 (VCC)
unnamed: C9.2, R3.1, U1.18 (VDDA)

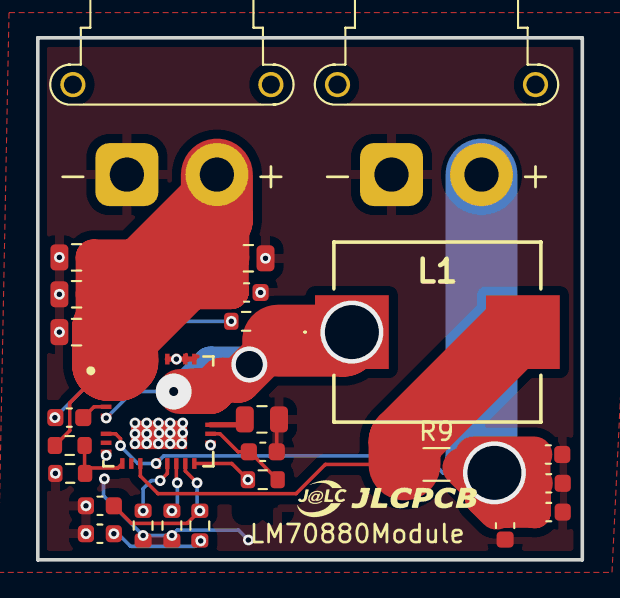
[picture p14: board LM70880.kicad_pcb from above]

Board: 2 copper layers, 30.2 x 29.0 mm, 26 parts (0 on the bottom side), 15 nets.

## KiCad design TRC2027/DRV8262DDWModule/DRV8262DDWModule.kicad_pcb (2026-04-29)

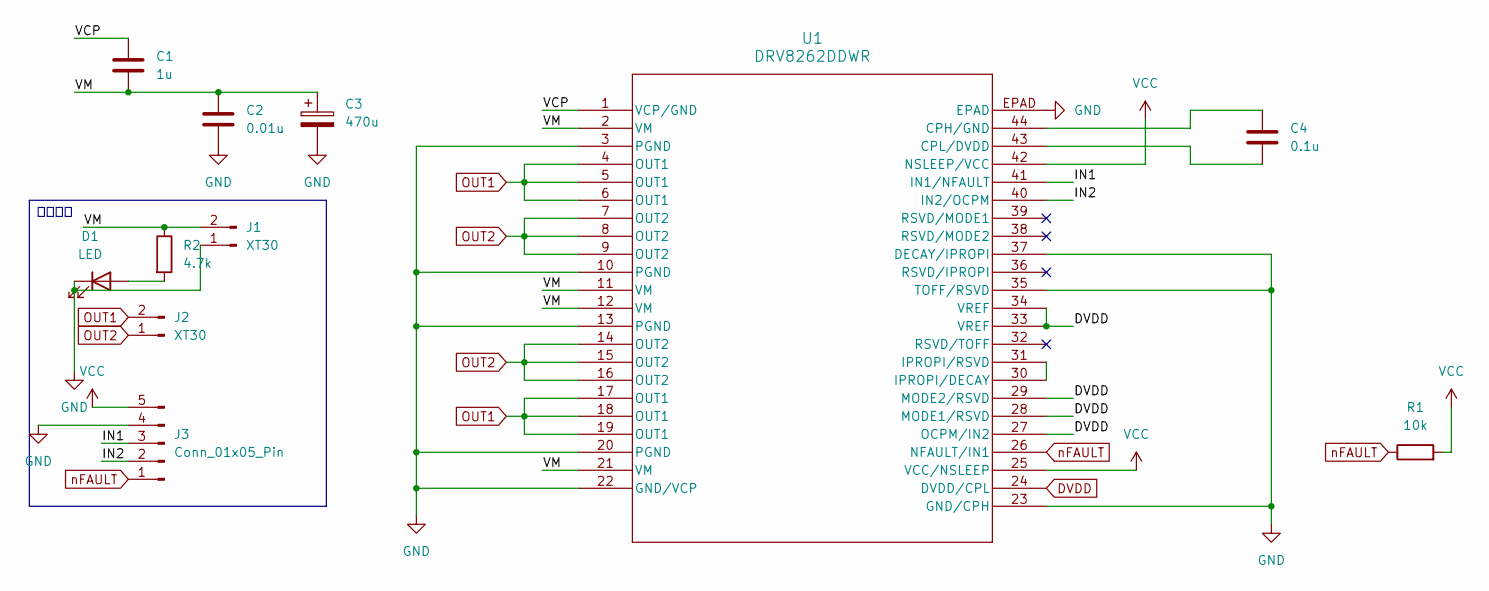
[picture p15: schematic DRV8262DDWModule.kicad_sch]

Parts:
C1: 1u; C_0603_1608Metric
C2: 0.01u; C_0603_1608Metric
C3: 470u; CP_Radial_D10.0mm_P5.00mm
C4: 0.1u; C_0603_1608Metric
D1: LED; LED_D5.0mm
J1, J2: XT30; AMASS_XT30PW-F_1x02_P2.50mm_Horizontal
J3: Conn_01x05_Pin; JST_XH_B5B-XH-A_1x05_P2.50mm_Vertical
R1: 10k; R_1206_3216Metric
R2: 4.7k; R_Axial_DIN0207_L6.3mm_D2.5mm_P10.16mm_Horizontal
U1: DRV8262DDWR; HTSSOP44-DDW_TEX

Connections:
/IN1: J3.3, U1.41 (IN1/NFAULT)
/IN2: J3.2, U1.40 (IN2/OCPM)
/VCP: C1.1, U1.1 (VCP/GND)
/VM: C1.2, C2.1, C3.1, J1.2, R2.1, U1.2 (VM), U1.11 (VM), U1.12 (VM), U1.21 (VM)
DVDD: U1.24 (DVDD/CPL), U1.27 (OCPM/IN2), U1.28 (MODE1/RSVD), U1.29 (MODE2/RSVD), U1.33 (VREF), U1.34 (VREF)
GND: C2.2, C3.2, D1.1 (K), J1.1, J3.4, U1.3 (PGND), U1.10 (PGND), U1.13 (PGND), U1.20 (PGND), U1.22 (GND/VCP), U1.23 (GND/CPH), U1.35 (TOFF/RSVD), U1.37 (DECAY/IPROPI), U1.EPAD
unnamed: D1.2 (A), R2.2
unnamed: C4.1, U1.44 (CPH/GND)
unnamed: C4.2, U1.43 (CPL/DVDD)
unnamed: U1.30 (IPROPI/DECAY), U1.31 (IPROPI/RSVD)
OUT1: J2.2, U1.4 (OUT1), U1.5 (OUT1), U1.6 (OUT1), U1.17 (OUT1), U1.18 (OUT1), U1.19 (OUT1)
OUT2: J2.1, U1.7 (OUT2), U1.8 (OUT2), U1.9 (OUT2), U1.14 (OUT2), U1.15 (OUT2), U1.16 (OUT2)
VCC: J3.5, R1.2, U1.25 (VCC/NSLEEP), U1.42 (NSLEEP/VCC)
nFAULT: J3.1, R1.1, U1.26 (NFAULT/IN1)

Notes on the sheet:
コネクト

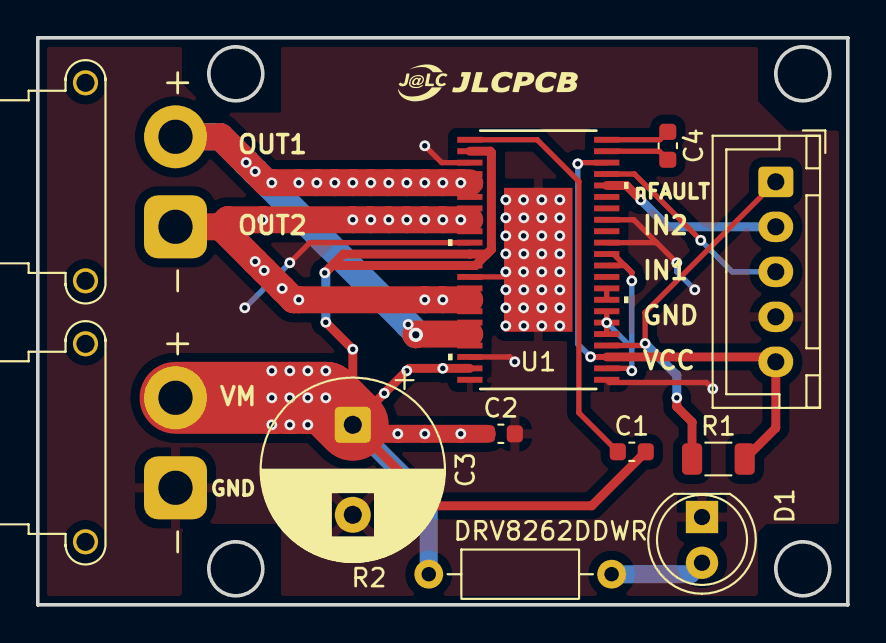
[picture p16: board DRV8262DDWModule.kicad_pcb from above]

Board: 2 copper layers, 45.0 x 31.5 mm, 11 parts (0 on the bottom side), 14 nets.

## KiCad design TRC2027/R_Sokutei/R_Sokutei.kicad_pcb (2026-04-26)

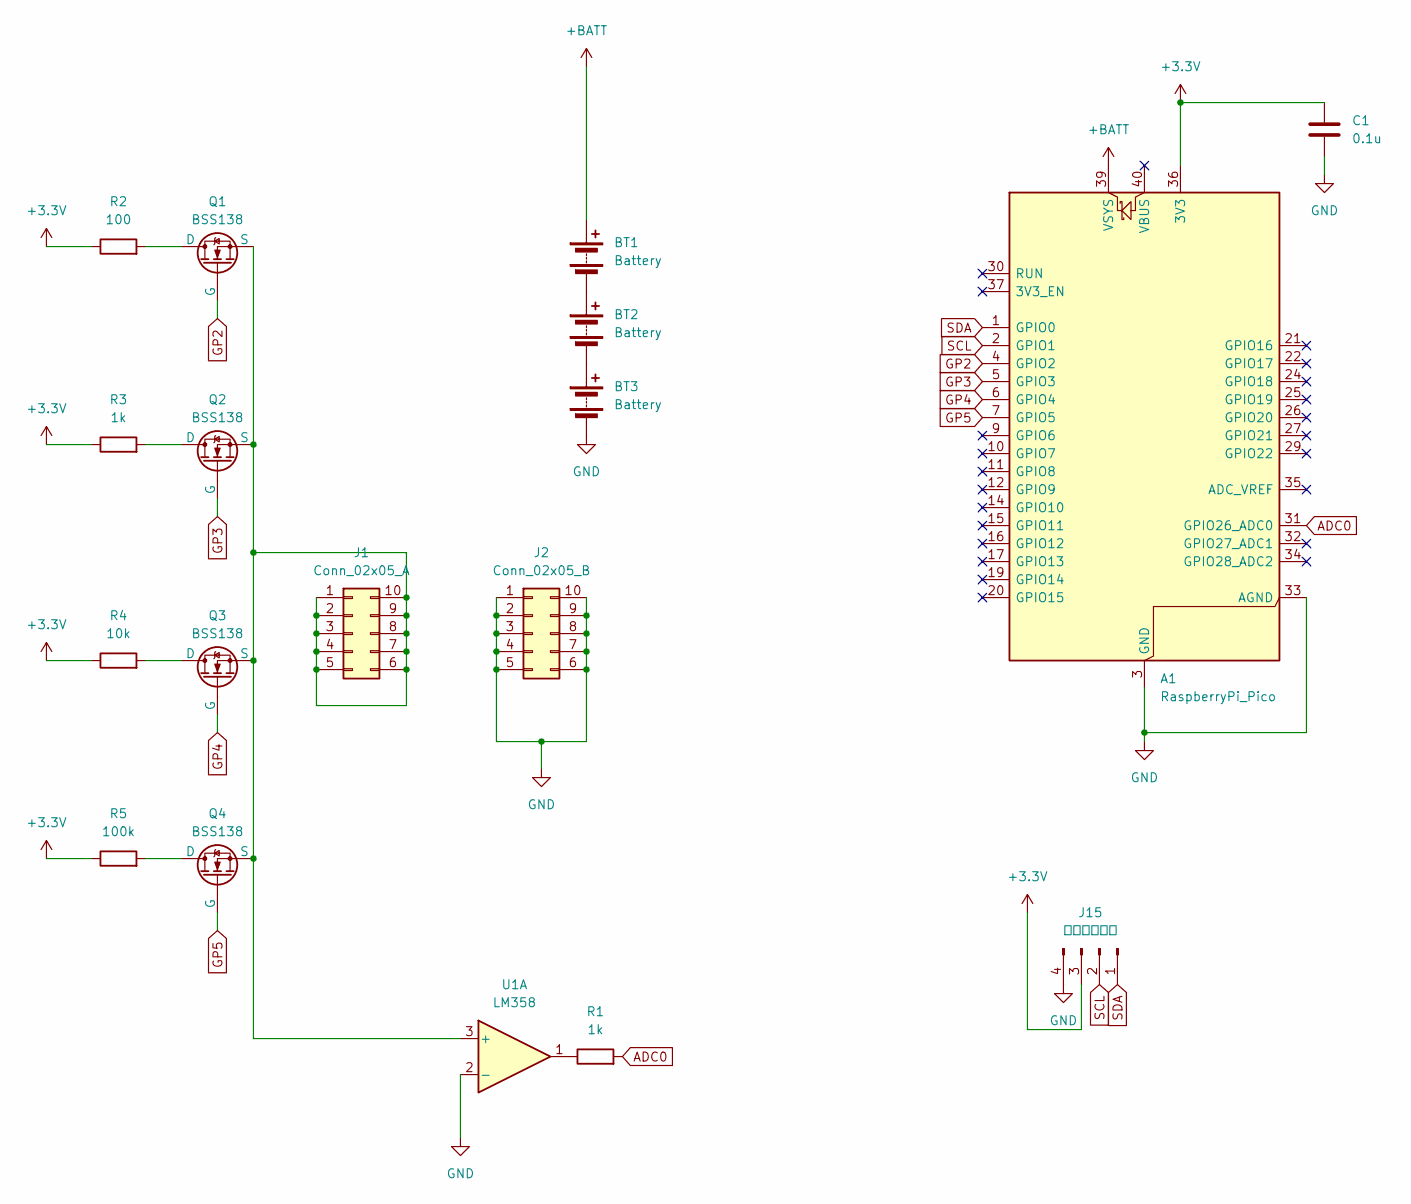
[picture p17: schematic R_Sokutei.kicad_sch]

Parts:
A1: RaspberryPi_Pico; RaspberryPi_Pico_Common_Unspecified
BT1, BT2, BT3: Battery; BatteryHolder_Keystone_2460_1xAA
C1: 0.1u; C_0603_1608Metric
J1: Conn_02x05_A; PinHeader_2x05_P2.54mm_Vertical
J2: Conn_02x05_B; PinHeader_2x05_P2.54mm_Vertical
J15: ディスプレイ; PinSocket_1x04_P2.54mm_Vertical
Q1, Q2, Q3, Q4: BSS138; SOT-23
R1, R3: 1k; R_Axial_DIN0207_L6.3mm_D2.5mm_P10.16mm_Horizontal
R2: 100; R_Axial_DIN0207_L6.3mm_D2.5mm_P10.16mm_Horizontal
R4: 10k; R_Axial_DIN0207_L6.3mm_D2.5mm_P10.16mm_Horizontal
R5: 100k; R_Axial_DIN0207_L6.3mm_D2.5mm_P10.16mm_Horizontal
U1: LM358; DIP-8_W7.62mm

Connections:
+3.3V: A1.36 (3V3), C1.1, J15.3, R2.1, R3.1, R4.1, R5.1
+BATT: A1.39 (VSYS), BT1.1 (+)
ADC0: A1.31 (GPIO26_ADC0), R1.2
GND: A1.3 (GND), A1.8 (GND), A1.13 (GND), A1.18 (GND), A1.23 (GND), A1.28 (GND), A1.33 (AGND), A1.38 (GND), BT3.2 (-), C1.2, J2.1, J2.2, J2.3, J2.4, J2.5, J2.6, J2.7, J2.8, J2.9, J2.10, J15.4, U1.2 (-)
GP2: A1.4 (GPIO2), Q1.2 (G)
GP3: A1.5 (GPIO3), Q2.2 (G)
GP4: A1.6 (GPIO4), Q3.2 (G)
GP5: A1.7 (GPIO5), Q4.2 (G)
unnamed: BT1.2 (-), BT2.1 (+)
unnamed: BT2.2 (-), BT3.1 (+)
unnamed: J1.1, J1.2, J1.3, J1.4, J1.5, J1.6, J1.7, J1.8, J1.9, J1.10, Q1.3 (S), Q2.3 (S), Q3.3 (S), Q4.3 (S), U1.3 (+)
unnamed: Q1.1 (D), R2.2
unnamed: Q2.1 (D), R3.2
unnamed: Q3.1 (D), R4.2
unnamed: Q4.1 (D), R5.2
unnamed: R1.1, U1.1
SCL: A1.2 (GPIO1), J15.2
SDA: A1.1 (GPIO0), J15.1

Board: 2 copper layers, 18 parts (0 on the bottom side), 18 nets, no tracks yet.

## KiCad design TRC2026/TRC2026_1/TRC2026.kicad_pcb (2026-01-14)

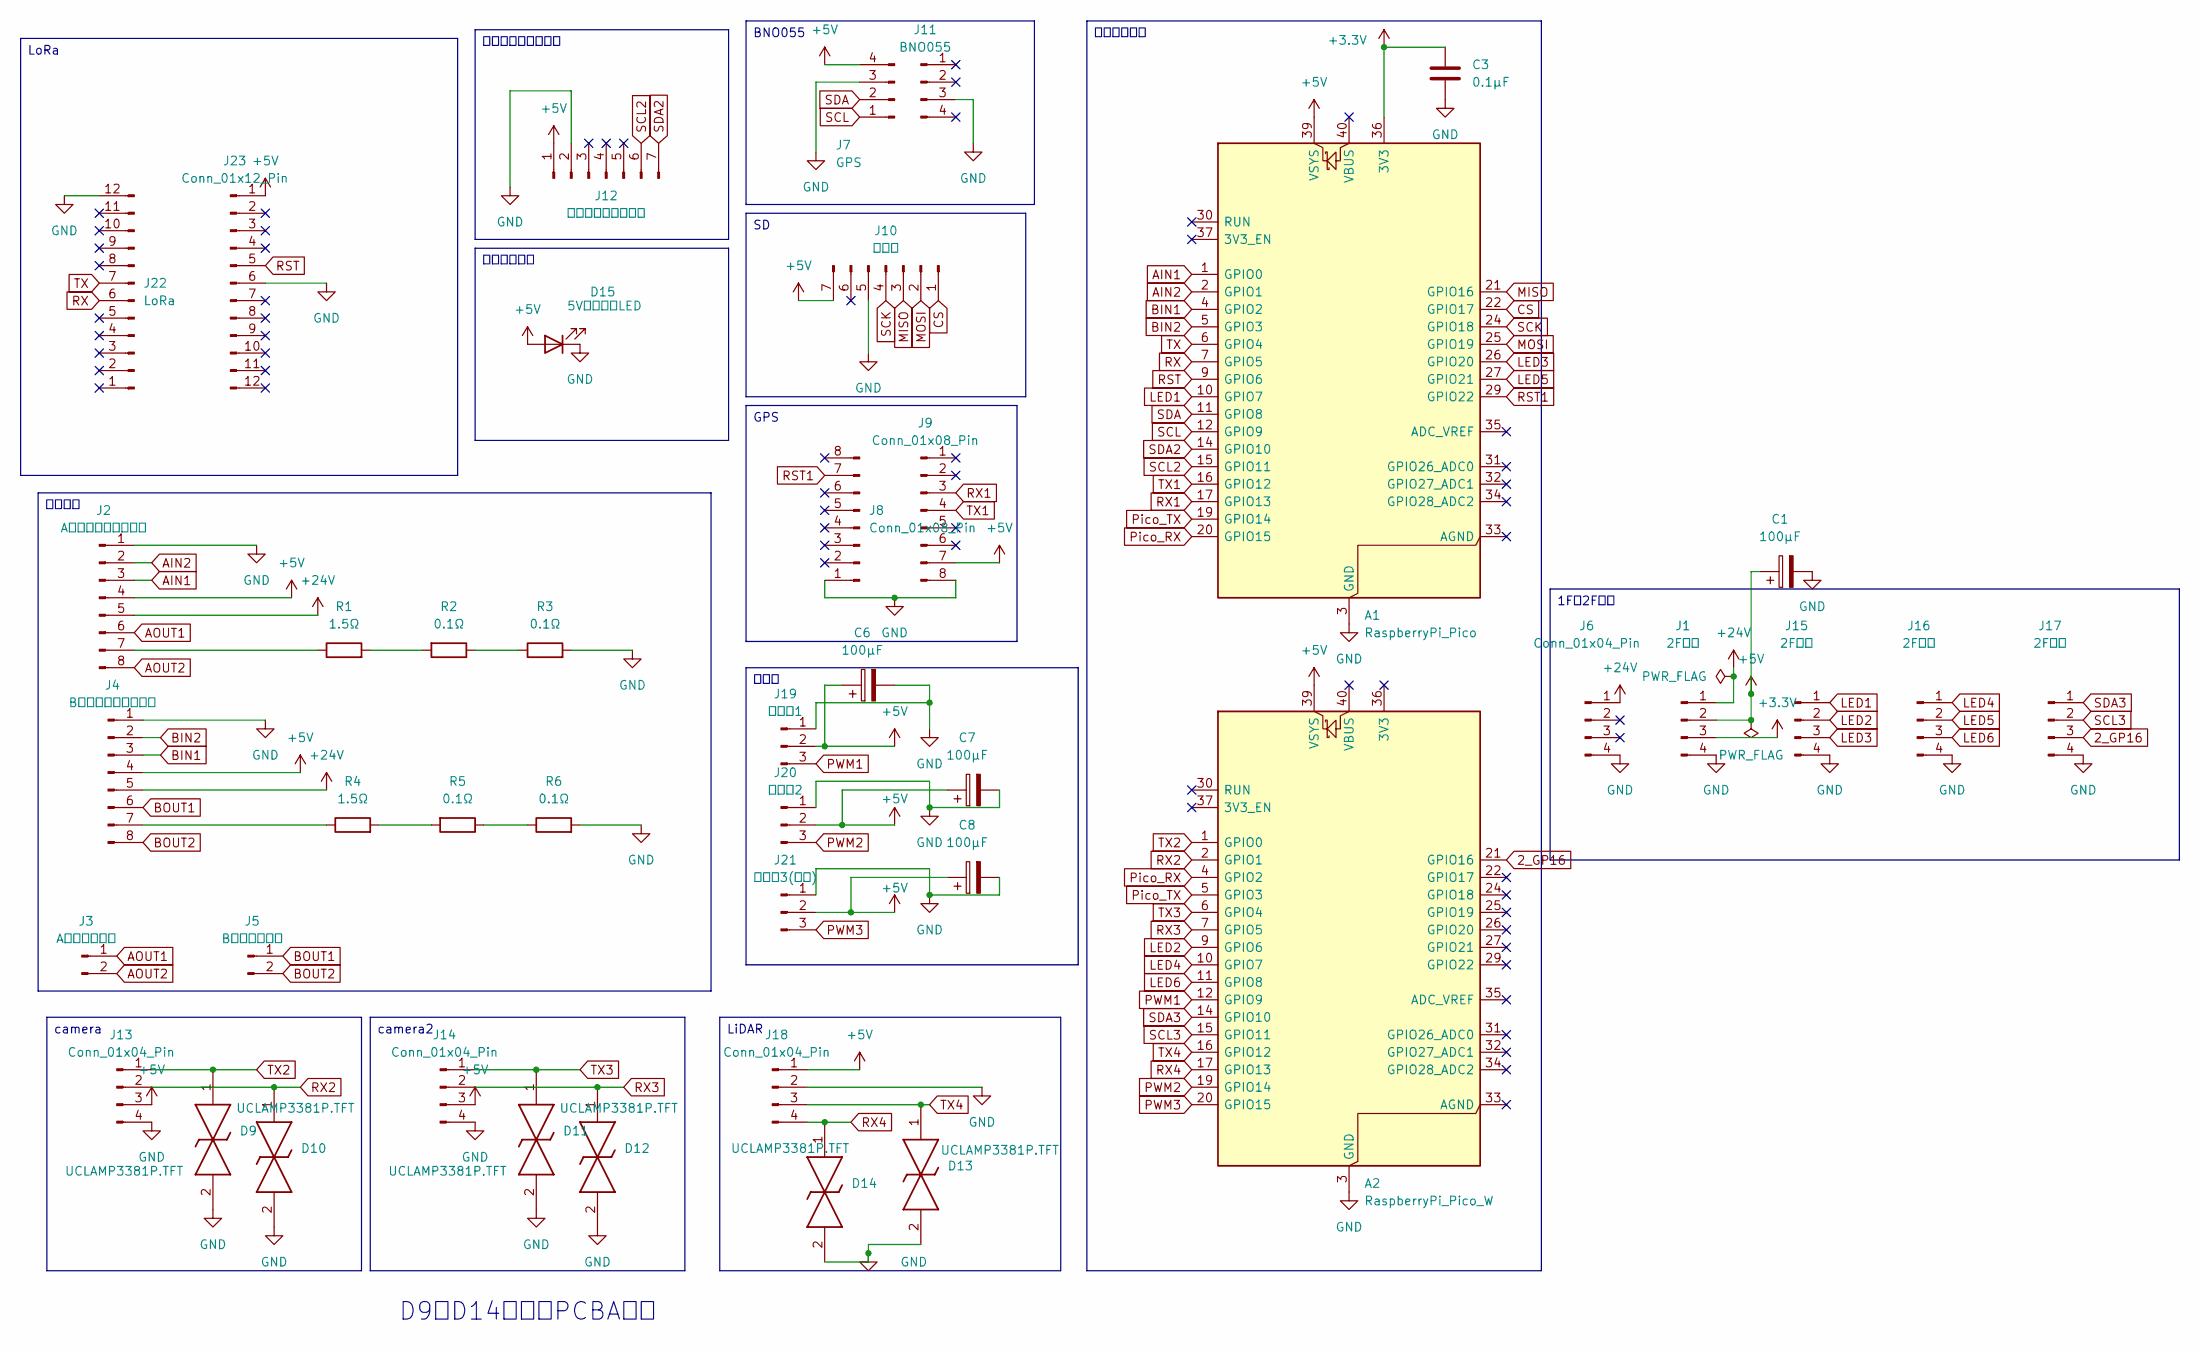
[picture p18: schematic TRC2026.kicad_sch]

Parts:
A1: RaspberryPi_Pico; RaspberryPi_Pico_Common_Unspecified
A2: RaspberryPi_Pico_W; RaspberryPi_PicoW_Common_THT
C1, C6, C7, C8: 100μF; CP_Radial_D8.0mm_P3.50mm
C3: 0.1μF; C_0603_1608Metric
D9, D10, D11, D12, D13, D14: UCLAMP3381P.TFT; SOD2513X114N; Mouser Part Number 947-UCLAMP3381P.TFT
D15: 5V抵抗内蔵LED; LED_D5.0mm
J1, J15, J16, J17: 2F接続; PinHeader_1x04_P2.54mm_Vertical
J2: Aモータードライバー; PinHeader_1x08_P2.54mm_Vertical
J3: Aモーター出力; JST_XH_B2B-XH-A_1x02_P2.50mm_Vertical
J4: Bモータードライバー; PinHeader_1x08_P2.54mm_Vertical
J5: Bモーター出力; JST_XH_B2B-XH-A_1x02_P2.50mm_Vertical
J6: Conn_01x04_Pin; PinHeader_1x04_P2.54mm_Vertical
J7: GPS; PinSocket_1x04_P2.54mm_Vertical
J8, J9: Conn_01x08_Pin; PinHeader_1x08_P2.54mm_Vertical
J10: メモリ; PinSocket_1x07_P2.54mm_Vertical
J11: BNO055; PinSocket_1x04_P2.54mm_Vertical
J12: 気温気圧高度センサ; PinSocket_1x07_P2.54mm_Vertical
J13, J14, J18: Conn_01x04_Pin; JST_XH_B4B-XH-A_1x04_P2.50mm_Vertical
J19: サーボ1; JST_XH_B3B-XH-A_1x03_P2.50mm_Vertical
J20: サーボ2; JST_XH_B3B-XH-A_1x03_P2.50mm_Vertical
J21: サーボ3(予備); JST_XH_B3B-XH-A_1x03_P2.50mm_Vertical
J22: LoRa; PinSocket_1x12_P2.54mm_Vertical
J23: Conn_01x12_Pin; PinSocket_1x12_P2.54mm_Vertical
R1, R4: 1.5Ω; R_Axial_DIN0207_L6.3mm_D2.5mm_P10.16mm_Horizontal
R2, R3, R5, R6: 0.1Ω; R_1210_3225Metric

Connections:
2_GP16: A2.21 (GPIO16), J17.3
+3.3V: A1.36 (3V3), C3.1, J1.3
+5V: A1.39 (VSYS), A2.39 (VSYS), C1.1, C6.1, C7.1, C8.1, D15.2 (A), J1.2, J2.4, J4.4, J7.4, J9.7, J10.7, J12.1, J13.3, J14.3, J18.1, J19.2, J20.2, J21.2, J23.1
+24V: J1.1, J2.5, J4.5, J6.1
AIN1: A1.1 (GPIO0), J2.3
AIN2: A1.2 (GPIO1), J2.2
AOUT1: J2.6, J3.1
AOUT2: J2.8, J3.2
BIN1: A1.4 (GPIO2), J4.3
BIN2: A1.5 (GPIO3), J4.2
BOUT1: J4.6, J5.1
BOUT2: J4.8, J5.2
CS: A1.22 (GPIO17), J10.1
GND: A1.3 (GND), A1.8 (GND), A1.13 (GND), A1.18 (GND), A1.23 (GND), A1.28 (GND), A1.38 (GND), A2.3 (GND), A2.8 (GND), A2.13 (GND), A2.18 (GND), A2.23 (GND), A2.28 (GND), A2.38 (GND), C1.2, C3.2, C6.2, C7.2, C8.2, D9.2, D10.2, D11.2, D12.2, D13.2, D14.2, D15.1 (K), J1.4, J2.1, J4.1, J6.4, J7.3, J8.1, J9.8, J10.5, J11.3, J12.2, J13.4, J14.4, J15.4, J16.4, J17.4, J18.2, J19.1, J20.1, J21.1, J22.12, J23.6, R3.2, R6.2
LED1: A1.10 (GPIO7), J15.1
LED2: A2.9 (GPIO6), J15.2
LED3: A1.26 (GPIO20), J15.3
LED4: A2.10 (GPIO7), J16.1
LED5: A1.27 (GPIO21), J16.2
LED6: A2.11 (GPIO8), J16.3
MISO: A1.21 (GPIO16), J10.3
MOSI: A1.25 (GPIO19), J10.2
unnamed: J2.7, R1.1
unnamed: J4.7, R4.1
unnamed: R1.2, R2.2
unnamed: R2.1, R3.1
unnamed: R4.2, R5.2
unnamed: R5.1, R6.1
PWM1: A2.12 (GPIO9), J19.3
PWM2: A2.19 (GPIO14), J20.3
PWM3: A2.20 (GPIO15), J21.3
Pico_RX: A1.20 (GPIO15), A2.4 (GPIO2)
Pico_TX: A1.19 (GPIO14), A2.5 (GPIO3)
RST: A1.9 (GPIO6), J23.5
RST1: A1.29 (GPIO22), J8.7
RX: A1.7 (GPIO5), J22.6
RX1: A1.17 (GPIO13), J9.3
RX2: A2.2 (GPIO1), D10.1, J13.2
RX3: A2.7 (GPIO5), D12.1, J14.2
RX4: A2.17 (GPIO13), D14.1, J18.4
SCK: A1.24 (GPIO18), J10.4
SCL: A1.12 (GPIO9), J7.1
SCL2: A1.15 (GPIO11), J12.6
SCL3: A2.15 (GPIO11), J17.2
SDA: A1.11 (GPIO8), J7.2
SDA2: A1.14 (GPIO10), J12.7
SDA3: A2.14 (GPIO10), J17.1
TX: A1.6 (GPIO4), J22.7
TX1: A1.16 (GPIO12), J9.4
TX2: A2.1 (GPIO0), D9.1, J13.1
TX3: A2.6 (GPIO4), D11.1, J14.1
TX4: A2.16 (GPIO12), D13.1, J18.3

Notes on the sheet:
D9～D14まではPCBA必須
モータ系
LoRa
サーボ
1Fと2F接続
camera
GPS
camera2
気温高度気圧センサ
LiDAR
電源チェック
BNO055
マイコン処理

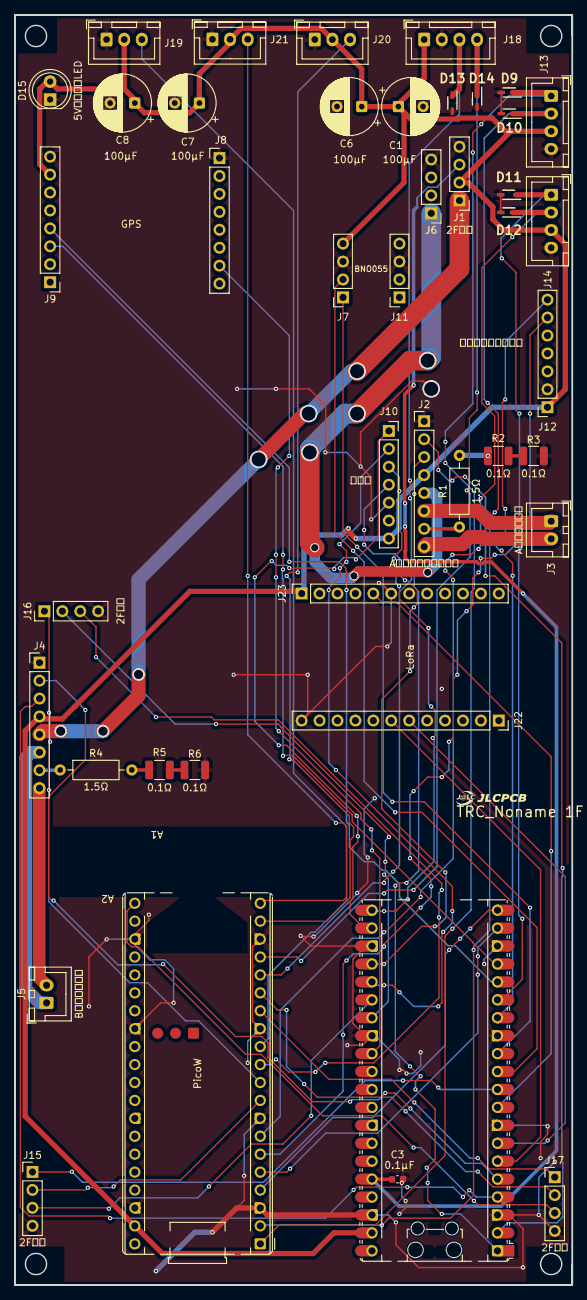
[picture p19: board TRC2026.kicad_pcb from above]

Board: 2 copper layers, 79.0 x 180.0 mm, 43 parts (0 on the bottom side), 52 nets.

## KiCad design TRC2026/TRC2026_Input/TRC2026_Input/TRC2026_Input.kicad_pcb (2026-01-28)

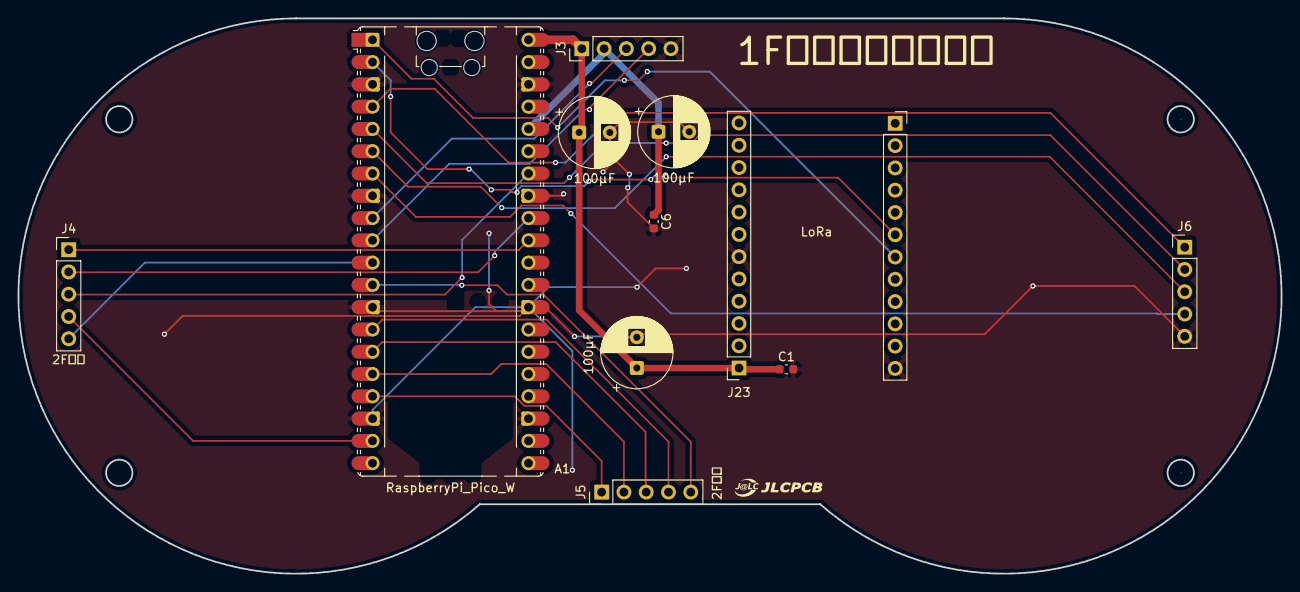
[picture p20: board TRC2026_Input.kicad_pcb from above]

Board: 2 copper layers, 144.0 x 63.3 mm, 12 parts (0 on the bottom side), 21 nets.

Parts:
A1: RaspberryPi_Pico_W; RaspberryPi_Pico_Common_Unspecified
C1, C6: 0.1μF; C_0603_1608Metric
C2, C4, C5: 100μF; CP_Radial_D8.0mm_P3.50mm
J3, J4, J5, J6: 2F接続; PinHeader_1x05_P2.54mm_Vertical
J22: LoRa; PinSocket_1x12_P2.54mm_Vertical
J23: Conn_01x12_Pin; PinSocket_1x12_P2.54mm_Vertical

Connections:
2_GP16: A1.19 (GPIO14), J4.4
+3.3V: A1.36 (3V3), C2.1, C6.1, J3.2
+5V: A1.40 (VBUS), C1.1, C4.1, C5.1, J3.1, J23.1
ADC0: A1.31 (GPIO26_ADC0), J4.1
ADC1: A1.32 (GPIO27_ADC1), J4.2
ADC2: A1.34 (GPIO28_ADC2), J4.3
GND: A1.3 (GND), A1.8 (GND), A1.13 (GND), A1.18 (GND), A1.23 (GND), A1.28 (GND), A1.33 (AGND), A1.38 (GND), C1.2, C2.2, C4.2, C5.2, C6.2, J3.5, J6.5, J22.12, J23.6
GP2: A1.4 (GPIO2), J6.1
GP3: A1.5 (GPIO3), J6.2
GP4: A1.6 (GPIO4), J6.3
GP5: A1.7 (GPIO5), J6.4
LED1: A1.11 (GPIO8), J4.5
LED2: A1.12 (GPIO9), J5.5
LED3: A1.14 (GPIO10), J5.4
LED4: A1.15 (GPIO11), J5.3
LED5: A1.16 (GPIO12), J5.2
LED6: A1.17 (GPIO13), J5.1
RX: A1.2 (GPIO1), J22.6
SCL3: A1.10 (GPIO7), J3.4
SDA3: A1.9 (GPIO6), J3.3
TX: A1.1 (GPIO0), J22.7

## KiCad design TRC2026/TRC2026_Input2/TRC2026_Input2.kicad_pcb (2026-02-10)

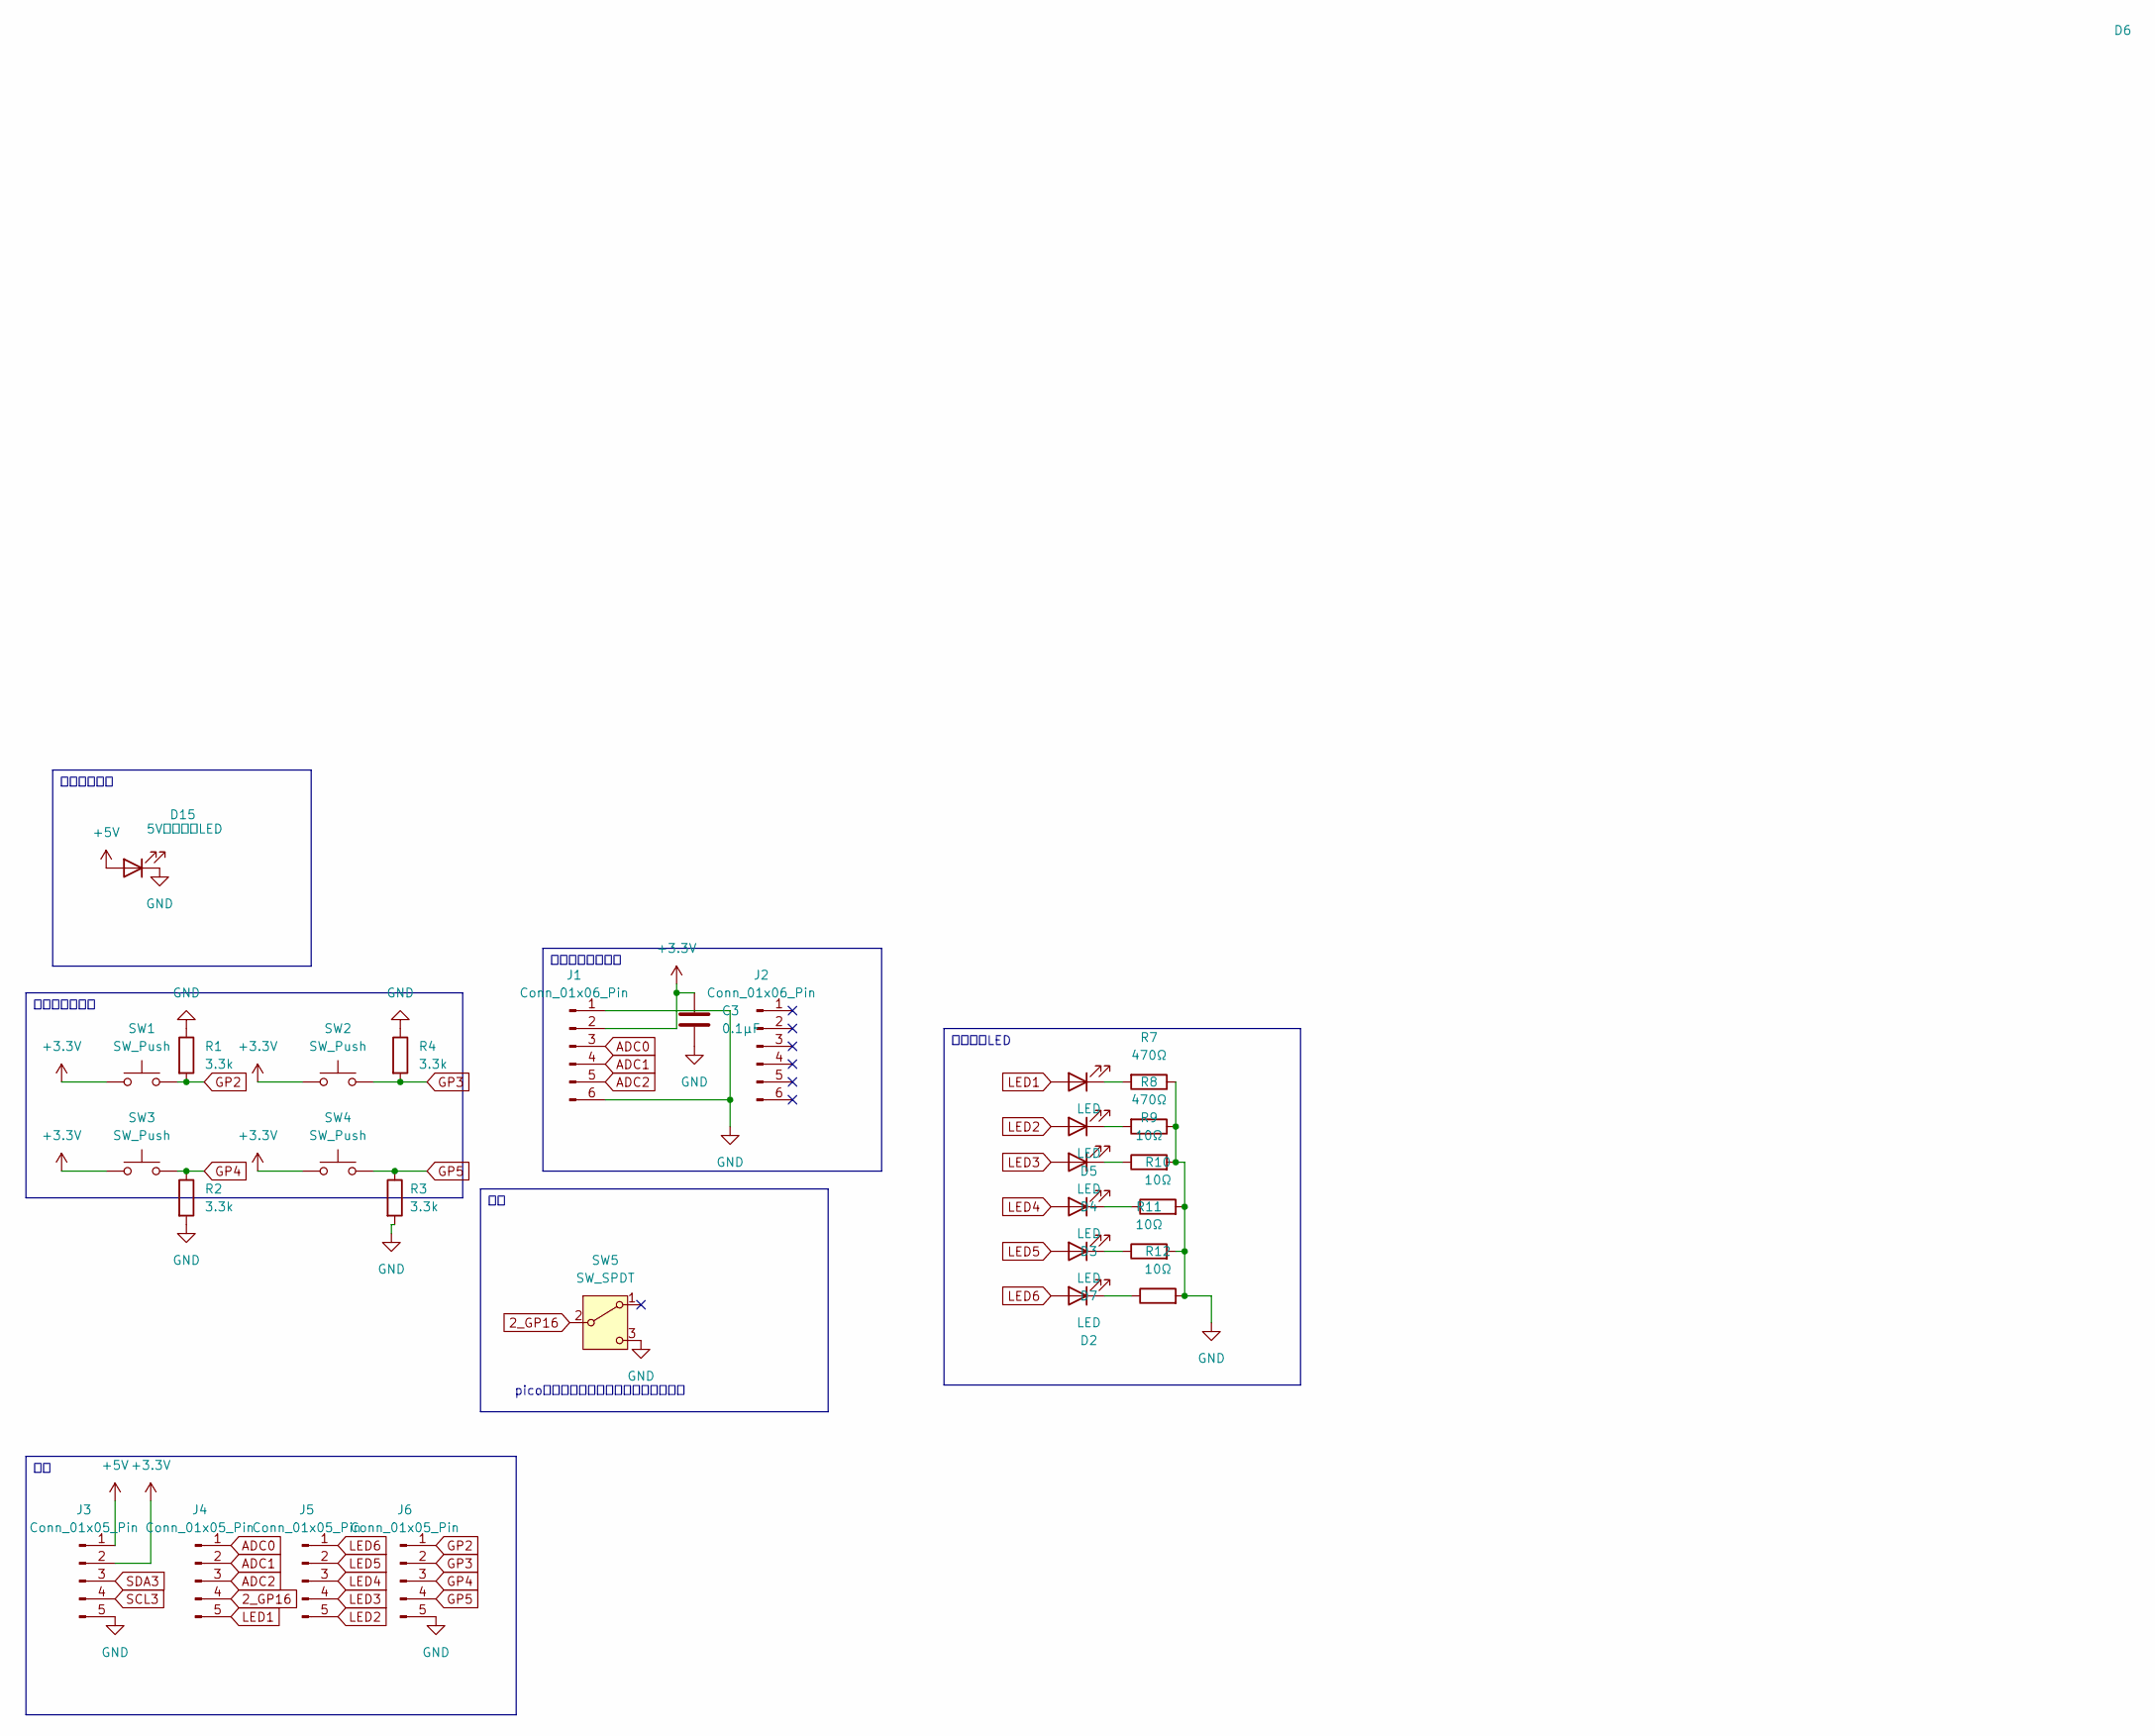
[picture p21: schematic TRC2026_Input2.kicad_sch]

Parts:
C3: 0.1μF; C_0603_1608Metric
D2, D3, D4, D5, D6, D7: LED; LED_D5.0mm
D15: 5V抵抗内蔵LED; LED_D5.0mm
J1, J2: Conn_01x06_Pin; PinHeader_1x06_P2.54mm_Vertical
J3, J4, J5, J6: Conn_01x05_Pin; PinHeader_1x05_P2.54mm_Vertical
R1, R2, R3, R4: 3.3k; R_Axial_DIN0207_L6.3mm_D2.5mm_P10.16mm_Horizontal
R7, R8: 470Ω; R_Axial_DIN0207_L6.3mm_D2.5mm_P10.16mm_Horizontal
R9, R10, R11, R12: 10Ω; R_Axial_DIN0207_L6.3mm_D2.5mm_P10.16mm_Horizontal
SW1, SW2, SW3, SW4: SW_Push; TVGP01G73BB
SW5: SW_SPDT; 3MS1J102M2QES

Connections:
2_GP16: J4.4, SW5.2 (B)
+3.3V: C3.1, J1.2, J3.2, SW1.1, SW2.1, SW3.1, SW4.1
+5V: D15.2 (A), J3.1
ADC0: J1.3, J4.1
ADC1: J1.4, J4.2
ADC2: J1.5, J4.3
GND: C3.2, D15.1 (K), J1.1, J1.6, J3.5, J6.5, R1.1, R2.2, R3.2, R4.1, R7.1, R8.1, R9.2, R10.2, R11.2, R12.2, SW5.3 (C); also elsewhere on the board
GP2: J6.1, R1.2, SW1.2; also elsewhere on the board
GP3: J6.2, R4.2, SW2.2
GP4: J6.3, R2.1, SW3.2
GP5: J6.4, R3.1, SW4.2
LED1: D6.2 (A), J4.5
LED2: D5.2 (A), J5.5
LED3: D4.2 (A), J5.4
LED4: D3.2 (A), J5.3
LED5: D7.2 (A), J5.2
LED6: D2.2 (A), J5.1
unnamed: D2.1 (K), R12.1
unnamed: D3.1 (K), R10.1
unnamed: D4.1 (K), R9.1
unnamed: D5.1 (K), R8.2
unnamed: D6.1 (K), R7.2
unnamed: D7.1 (K), R11.1
SCL3: J3.4
SDA3: J3.3

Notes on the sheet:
picoの内蔵プルアップ抵抗を入れること
電源チェック
ジョイスティック
タクトスイッチ
状態表示LED


Board: 2 copper layers, 144.0 x 63.3 mm, 29 parts (0 on the bottom side), 23 nets.

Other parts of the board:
10k: 3.3k; R_Axial_DIN0207_L6.3mm_D2.5mm_P10.16mm_Horizontal

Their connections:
GND: 10k.1; also elsewhere on the board
GP2: 10k.2; also elsewhere on the board

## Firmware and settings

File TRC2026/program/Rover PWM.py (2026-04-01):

from machine import UART, Pin, PWM
import time

# ===== ピン設定 =====
LORA_TX  = 4
LORA_RX  = 5
AIN1_PIN = 0
AIN2_PIN = 1
BIN1_PIN = 2
BIN2_PIN = 3
TIMEOUT_SEC = 2

# ===== 速度設定（0〜65535）=====
SPEED      = 65535
TURN_SPEED = 10000

# ===== LoRa UART =====
lora = UART(1, 9600)
lora.init(9600, bits=8, parity=None, stop=1, tx=Pin(LORA_TX), rx=Pin(LORA_RX))

# ===== PWMモーター =====
AIN1 = PWM(Pin(AIN1_PIN)); AIN1.freq(1000)
AIN2 = PWM(Pin(AIN2_PIN)); AIN2.freq(1000)
BIN1 = PWM(Pin(BIN1_PIN)); BIN1.freq(1000)
BIN2 = PWM(Pin(BIN2_PIN)); BIN2.freq(1000)

# ★ 全ピンをまとめて設定するヘルパー（書き忘れ防止）

"""モーター"""
AIN1 = PWM(Pin(2))
AIN2 = PWM(Pin(3))
BIN1 = PWM(Pin(1))
BIN2 = PWM(Pin(0))

AIN1.freq(20000)
AIN2.freq(20000)
BIN1.freq(20000)
BIN2.freq(20000)

def left_forward(speed):
    AIN1.duty_u16(0)
    AIN2.duty_u16(speed)

def left_backward(speed):
    AIN1.duty_u16(speed)
    AIN2.duty_u16(0)

def left_stop():
    AIN1.duty_u16(0)
    AIN2.duty_u16(0)


def right_forward(speed):
    BIN1.duty_u16(65535 - speed)
    BIN2.duty_u16(0)

def right_backward(speed):
    BIN1.duty_u16(65535)
    BIN2.duty_u16(65535)

def right_stop():
    BIN1.duty_u16(0)
    BIN2.duty_u16(0)


def motor_stop():
    left_stop()
    right_stop()

def motor_forward(speed):
    left_forward(speed)
    right_forward(speed)

def motor_backward(speed):
    left_backward(speed)
    right_backward(speed)
    
def _set(a1, a2, b1, b2):
    AIN1.duty_u16(a1)
    AIN2.duty_u16(a2)
    BIN1.duty_u16(65535 - b1)
    BIN2.duty_u16(b2 - 65535)

def forward():
    motor_forward(65535)

def backward():
    motor_backward(65535)

def turn_left():
    left_forward(10000)
    right_forward(65535)# Aのみ、Bは必ず0

def turn_right():
    left_forward(65535)
    right_forward(10000)   # Bのみ、Aは必ず0

def all_stop():
    motor_forward(0)

ACTIONS = {
    "M:FWD": (forward,    "前進"),
    "M:BCK": (backward,   "後進"),
    "M:LFT": (turn_left,  "左旋回(Aのみ)"),
    "M:RGT": (turn_right, "右旋回(Bのみ)"),
    "M:STP": (all_stop,   "停止"),
}

def send_command(cmd, wait_time=1):
    lora.write(cmd + "\r\n")
    time.sleep(wait_time)
    response = ""
    while lora.any():
        data = lora.read()
        try:
            response += data.decode()
        except:
            pass
    print("CMD: " + cmd + " -> " + response.strip())
    return response.strip()

def restart_rx():
    lora.write("AT+TEST=RXLRPKT\r\n")
    time.sleep(0.3)
    while lora.any():
        lora.read()

def check_received():
    if lora.any():
        data = lora.read()
        try:
            response = data.decode()
        except:
            return None
        if "+TEST: RX" in response:
            try:
                start = response.find('"')
                if start != -1:
                    start += 1
                    end = response.find('"', start)
                    if end != -1:
                        return bytes.fromhex(response[start:end]).decode()
            except Exception as e:
                print("解析エラー: " + str(e))
    return None

# ===== 初期化 =====
print("=== 機体側起動 (Pico / PWM) ===")
all_stop()
time.sleep(1)
send_command("AT")
send_command("AT+MODE=TEST")
send_command("AT+TEST=RFCFG,923,7,0,1,8,14", 0.5)
send_command("AT+TEST=RXLRPKT")
print("=== 受信待機中 ===\n")

# ===== メインループ =====
rx_count     = 0
last_rx_time = time.time()

while True:
    try:
        msg = check_received()
        if msg:
            msg = msg.strip()
            last_rx_time = time.time()
            rx_count += 1
            if msg in ACTIONS:
                action, label = ACTIONS[msg]
                action()
                print("[RX#" + str(rx_count) + "] " + label)
            else:
                print("[RX#" + str(rx_count) + "] 不明: " + msg)
            restart_rx()

        if time.time() - last_rx_time > TIMEOUT_SEC:
            all_stop()
            last_rx_time = time.time()
            print("[タイムアウト] 停止")

        time.sleep(0.05)

    except KeyboardInterrupt:
        all_stop()
        print("\n終了")
        break
    except Exception as e:
        print("エラー: " + str(e))
        all_stop()
        import sys
        sys.print_exception(e)

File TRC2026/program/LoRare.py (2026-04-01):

from machine import UART, Pin
import time

# LoRa UART設定（送信側と完全一致）
uart = UART(1, 9600)
uart.init(9600, bits=8, parity=None, stop=1, tx=Pin(4), rx=Pin(5))

def send_command(cmd, wait_time=1):
    """ATコマンド送信"""
    uart.write(cmd + "\r\n")
    time.sleep(wait_time)
    response = ""
    while uart.any():
    
        data = uart.read()
        try:
            response += data.decode()
        except:
            pass
    print("CMD: " + cmd + " -> " + response.strip())
    return response.strip()

def check_received():
    """受信データ確認"""
    if uart.any():
        data = uart.read()
        try:
            response = data.decode()
        except:
            return None, None

        if "+TEST: RX" in response:
            try:
                start = response.find('"')
                if start != -1:
                    start += 1
                    end = response.find('"', start)
                    if end != -1:
                        hex_data = response[start:end]
                        msg = bytes.fromhex(hex_data).decode()

                        rssi = "N/A"
                        if "RSSI" in response:
                            rssi_start = response.find("RSSI") + 4
                            rssi_end = response.find(",", rssi_start)
                            if rssi_end == -1:
                                rssi_end = response.find("\r", rssi_start)
                            if rssi_end != -1:
                                rssi = response[rssi_start:rssi_end].strip()

                        return msg, rssi
            except Exception as e:
                print("解析エラー: " + str(e))
                print("生データ: " + response)

    return None, None

# ===== 初期化（送信側のsetup()と完全一致）=====
print("=== LoRa受信機 ===\n")
time.sleep(1)
print("初期化中...")
print("\n--- 設定開始 ---")
send_command("AT")
send_command("AT+MODE=TEST")
send_command("AT+TEST=RFCFG,923,7,0,1,8,14", 0.5)  # ★送信側と完全一致
send_command("AT+TEST=RXLRPKT")
print("--- 設定完了 ---\n")

# ===== メインループ =====
print("=== 受信待機中 ===")
print("Ctrl+C で停止\n")

receive_count = 0

while True:
    try:
        msg, rssi = check_received()

        if msg:
            receive_count += 1
            print("[" + str(receive_count) + "] 受信: " + msg)
            if rssi != "N/A":
                print("    RSSI: " + rssi + " dBm")
            print()

        time.sleep(0.1)

    except KeyboardInterrupt:
        print("\n受信機停止")
        uart.write("AT+TEST=STOP\r\n")
        break
    except Exception as e:
        print("エラー: " + str(e))
        import sys
        sys.print_exception(e)

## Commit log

2026-01-04 回路図変えたよ
    [TRC2026.kicad_pcb, bom.csv, designators.csv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]
2026-01-14 基板をめちゃめちゃ修正しました
    [TRC2026.kicad_pcb, TRC2026.kicad_sch, TRC2026_2.kicad_pcb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]
2026-01-15 Create プログラム
2026-01-23 回路図系の更新
    [TRC2026_2.kicad_sch, TRC2026_Input.kicad_pcb, TRC2026_Input.kicad_sch]
2026-01-28 いろいろと変更
    [TRC2026_Input.kicad_pcb, TRC2026_Input.kicad_sch, TRC2026_Input2.kicad_pcb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]
2026-01-29 変更しちゃった
2026-02-06 LIdarテストプログラム
2026-02-06 GPSのテストプログラム
2026-02-07 add GPS_henkan
    [coordinates.csv]
2026-02-10 プルダウン抵抗とフットプリントを修正しました
    [TRC2026_2.kicad_pcb, TRC2026_2.kicad_sch, TRC2026_Input2.kicad_pcb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]
2026-03-12 回路図修正
2026-03-13 ラジコン
2026-03-18 ラジコン操作のプログラム
2026-03-19 LoRaだけの通信プログラム
2026-03-20 機体側のPWM制御のラジコン
2026-04-01 いろいろ追加
    [24FC1025-I_P.stp, 3557-15.step, AE-DRV8835-S.stp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]
2026-04-01 add LTE_Module
    [TRC2027main.kicad_sch]
2026-04-04 change DataSheet
    [TRC2027main.kicad_sch]
2026-04-18 add TRC2027main/SW_LED
    [3557-15.step, TRC2027main.kicad_sch]
2026-04-26 new file: TRC2027/R_Sokutei/R_Sokutei-backups/R_Sokutei-2026-04-18_181141.zip
    [OKL-T_6-W12N-C.step, R_Sokutei.kicad_pcb, R_Sokutei.kicad_sch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]
2026-06-23 Add positions.csv file with component placements and orientations
    [LM70880.kicad_pcb, LM70880.kicad_sch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]
